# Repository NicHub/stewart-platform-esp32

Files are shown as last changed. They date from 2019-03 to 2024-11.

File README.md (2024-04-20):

# STEWART PLATFORM ON ESP32

<a href="https://archiveprogram.github.com/arctic-vault/">
<table style="border:none">
<tr>
<td>

</td>
<td>
This repository<br/>is archived in the<br/><em>GitHub Arctic Code Vault</em>.
</td>
</tr>
</table>
</a>

<p align="center">
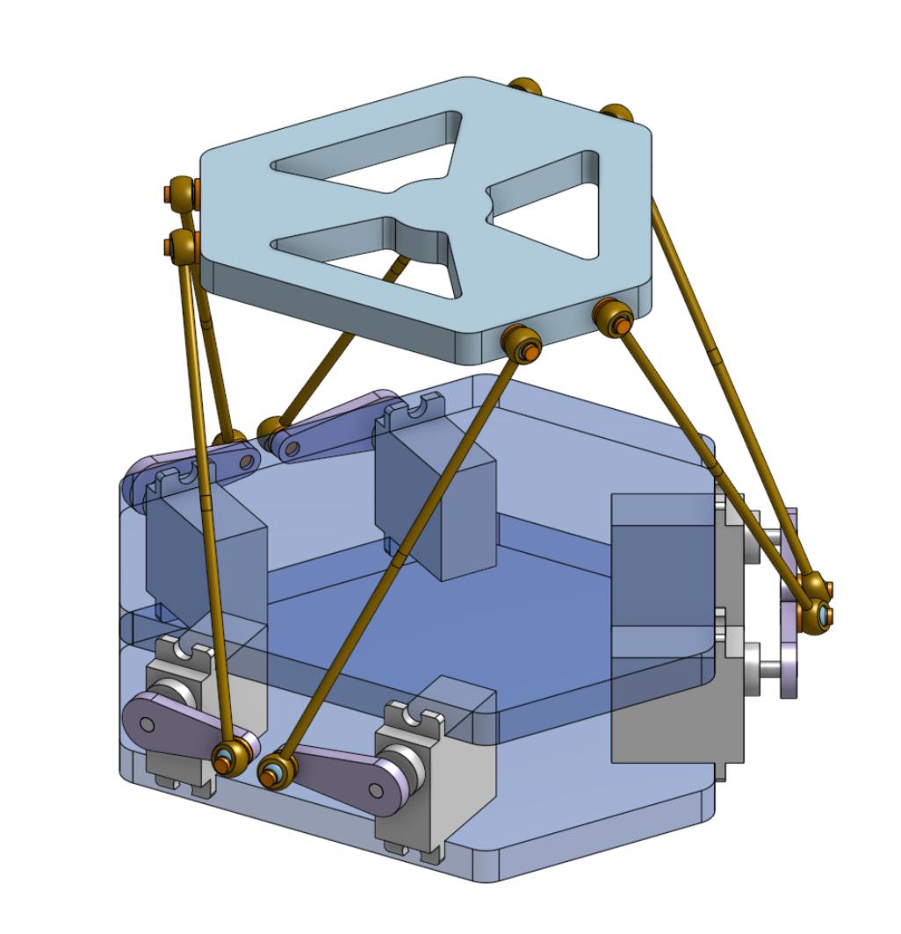
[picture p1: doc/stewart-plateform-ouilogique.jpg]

</p>

## ABSTRACT

This is an ESP32 implementation of a six-degree-of-freedom hexapod — also called _Stewart Platform_, _Gough-Stewart Platform_ or _Parallel manipulator_.
The actuators are PWM rotary servo motors and the program is written in _Arduino C_ compiled with [_PlatformIO_](https://platformio.org/).
This project is done in the frame of the _P19 project_ at the [Microclub](https://microclub.ch).

Currently the platform can be operated:

-   With a _Nunchuck_.
-   With _Arduino C_ code (see [`Hexapod_Demo.cpp`](./src/Hexapod_Demo.cpp)).
-   With _G-Code_ sent by a computer to the ESP through the serial port (see [`python/gcode2serial.py`](./gcode2serial/gcode2serial.py)).

The calculation of the kinematics is performed in [`Hexapod_Kinematics.cpp`](./src/Hexapod_Kinematics.cpp) and can be also be compiled in a desktop C++ program to cross-check calculations (i.e. without actuating the servos).
I managed to compile it with `g++` on _macOS Mojave_ and _macOS Monterey_.
See [`hexapod_desktop_app/hexapod_desktop_app.cpp`](./hexapod_desktop_app_cpp/hexapod_desktop_app.cpp).

## HOME PAGE OF THE PROJECT

The home page is a work in progress, but the video shows what the platform can do.
The original implementation used an analog joystick, but the current version uses a Wii Nunchuck.

The automatic translation in English can be read here:

<https://ouilogique-com.translate.goog/plateforme-de-stewart-esp32/?_x_tr_sl=fr&_x_tr_tl=en>

The original version in French is here:

<https://ouilogique.com/plateforme-de-stewart-esp32/>

## PREREQUISITES

-   Change the default I²C address of the PCA9685 driver from `0x40` to `0x41` by shorting the A0 jumper beside the capacitor.

<p align="center">
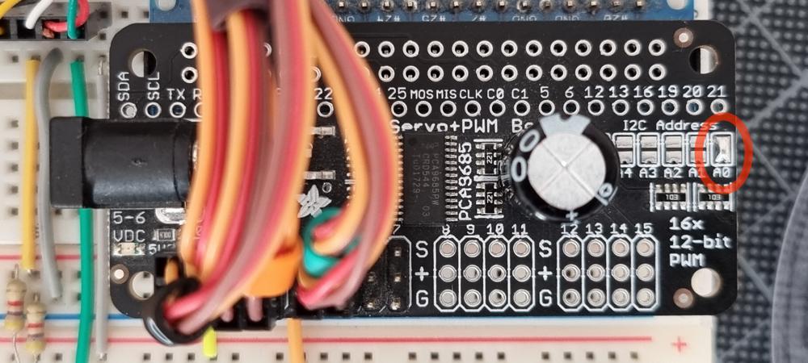
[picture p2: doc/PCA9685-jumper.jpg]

</p>

-   Create a file called `src/WifiSettings.h` containing:

```C++
#pragma once

const char *ssid = "";            // SSID of your WiFi router.
const char *password = "";        // Password of your WiFi router.
const char *ap_ssid = "STEW32-";  // SSID of the ESP32 WiFi network in soft-AP mode (15 char max).
const char *ap_password = "";     // Password of the ESP32 WiFi network in soft-AP mode.
                                  // Must be 8 char min or empty for no password.
```

## GEOMETRY SETTINGS

Geometry settings are defined in
[`Hexapod_Config_1.h`](./src/Hexapod_Config_1.h).

The meaning of the parameters is explained in
[`doc/hexapod-parameters.pdf`](./doc/hexapod-parameters.pdf).

## PARTS TO BUILD

### Base plates

The two base plates are identical and the DXF file to reproduce them is here (right-click + save as):
[`doc/hexapod-base-plate.dxf`](https://raw.githubusercontent.com/NicHub/stewart-platform-esp32/master/doc/hexapod-base-plate.dxf).

<p align="center">
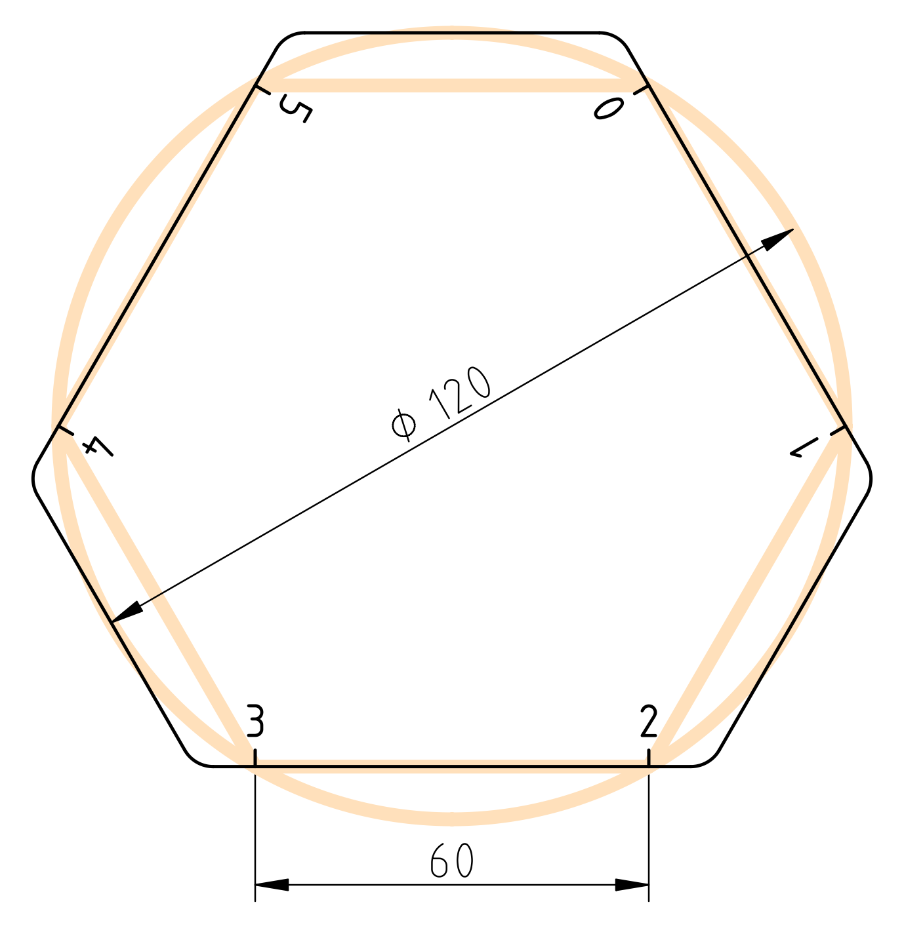
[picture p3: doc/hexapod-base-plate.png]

</p>

### Top plate

The top plate is 3D-printed (right-click + save as):
[`doc/hexapod-top-plate.stl.zip`](https://raw.githubusercontent.com/NicHub/stewart-platform-esp32/master/doc/hexapod-top-plate.stl.zip).

## PARTS TO BUY

| QTY  | PART |
| :--- | :--- |
| 1 | [WeMos ESP32 WROOM](https://www.banggood.com/fr/WeMos-ESP32-WiFi-Bluetooth-Development-Board-Ultra-Low-Power-Consumption-Dual-Core-ESP-32-ESP-32S-p-1175488.html) |
| 1 | [Adafruit PCA9685 16-Channel Servo I²C Driver](https://www.mouser.ch/ProductDetail/adafruit/3416/?qs=F5EMLAvA7ICYzX4Av%252bhRHw==) |
| 1 | [Breadboard adapter for PCA9685](https://www.aliexpress.com/item/1005004132188471.html) |
| 1 | [5 V / 10 A power supply](https://aliexpress.com/af/32810906485.html) |
| 6 | [Rods M3x100mm (140mm total)](https://aliexpress.com/af/32775630549.html) |
| 6 | ¹ [Tower Pro MG996R servo (clone)](https://fr.aliexpress.com/item/32636102294.html) |
| 1 | [Nunchuck](https://fr.aliexpress.com/item/1005003050706988.html) <!-- https://fr.aliexpress.com/item//32880983134.html --> |
| 1 | ² [Nunchuck cable extension](https://fr.aliexpress.com/item/32784720613.html) <!-- https://fr.aliexpress.com/item//32841281892.html --> |
| 1 | ³ [Adafruit Wii Nunchuck Breakout Adapter](https://www.adafruit.com/product/4836) |
| 1 | [6 pin Dupont connector to connect Nunchuck to breadboard](https://www.aliexpress.com/item/32809965211.html) |
| 1 | [Set of cable markers](https://fr.aliexpress.com/item/1005004255868271.html) |
| 6 | [M3×5×6 Brass insert nuts](https://www.aliexpress.com/item/32828848326.html) |
| 12 | Small screws to hold the motors on the base plates |
| 6 | M3×12 screw |
| 6 | M3×12 nut |
| 1 | Breadboard |
| some | Breadboard wires |
| 2 | 4.7 kΩ resistor |

### Notes

-   ¹ I currently use clones of the _Tower Pro MG996R_ servos, but they are bad and I don’t recommend them.
    <https://fr.aliexpress.com/item/32636102294.html><br/>
    I formerly used clones of the _Tower Pro MG90s_ Servos, but they were also bad and too small for this application.
    <https://www.banggood.com/6X-Towerpro-MG90S-Metal-Gear-RC-Micro-Servo-p-1072260.html><br/>
    In the future, I will probalbly use _Parallax 900-00005_ servos.
    It seems that these are the one used by _fullmotiondynamics_ in their videos.
    <https://www.parallax.com/product/900-00005>
-   ² The Nunchuck cable extension is not mandatory.
    The idea is not to have a longer cable but rather to use the extension as an adapter between the Nunchuck and the breadboard, that is to say that it allows to leave the Nunchunk cable uncut.
-   ³ This breakout adapter is not mandatory, but it could simplify wiring.
    I haven’t used it myself.

## WIRING

### Nunchuck

> The Nunchuck library uses `Wire.h` and standard I²C connections internaly.
>
> Pins are seen from left to right and top to bottom looking at the Nunchuck connector.
>
> Cut the cable extension to connect to the ESP32.

| color  | signal | ESP32 pin |
| :----- | :----- | :--- |
| white  | SCL | IO22 |
| NC | | |
| red | GND | GND |
| green  | VCC | VCC |
| black  | ATT | IO32 (or connect to 3.3V to force Nunchunk detection) |
| yellow | SDA | IO21 |

## EXTERNAL LIBRARIES

The external libraries are installed automatically during the first build because they are declared under `lib_deps` in `platformio.ini`.

## I²C ADDRESSES

> By default, the PCA9685 driver and the Nunchuck share the same I²C address `0x40`.
> Fortunately, the address of the PCA9685 driver can easily be changed to `0x41` by shorting the A0 jumper next to the capacitor.

| Default address | New address | Device |
| :--- | :--- | :--- |
| 0x40 | 0x41 | PCA9685 |
| 0x70 | = | PCA9685 (broadcast) |
| 0x40 | = | Nunchuck ([IMU](https://en.wikipedia.org/wiki/Inertial_measurement_unit)) |
| 0x52 | = | Nunchuck (joystick) |
| 0x68 | = | GY-91 (MPU9250) |
| 0x76 | = | GY-91 (BMP280) |

## CREDITS

### My sources of inspiration

-   San-José State University / Full Motion Dynamics:
    -   <https://www.youtube.com/watch?v=j4OmVLc_oDw>
    -   ~~fullmotiondynamics.com~~

### Kinematics

-   Hexapod kinematics of this project was originaly based on _6dof-stewduino, by Philippe Desrosiers_, althought I reworked it in depth:
    -   <https://github.com/xoxota99/stewy>
-   He derived his implementation from the work of _Daniel Waters_:
    -   <https://www.youtube.com/watch?v=1jrP3_1ML9M>
-   Kinematics calculation is also explained in this document by an unknown author from the _Wokingham U3A Math Group_:
    -   <https://memememememememe.me/assets/posts/stewart-platform-math/MathsOfStewartPlatformV5.pdf>
    -   <http://www.wokinghamu3a.org.uk/groups/mathematics/>
-   The project _memememememememe_ was also an excellent source of inspiration.
    They share the code for _RPi_ and a simulator in the _Processing_ langage:
    -   <https://memememememememe.me/post/stewart-platform-math/>
    -   <https://github.com/thiagohersan/memememe>

### Serial buffer for G-Code

-   Derived from _MarginallyClever_:
    -   <https://github.com/MarginallyClever/GcodeCNCDemo/tree/master/GcodeCNCDemo4AxisCNCShield>

## FURTHER READINGS

-   PID Control System Analysis and Design, By YUN LI, KIAM HEONG ANG, and GREGORY C.Y. CHONG
    -   See Table 1, p.33 <http://eprints.gla.ac.uk/3815/1/IEEE_CS_PID_01580152.pdf>
-   Understanding PID Control, Part 1: What is PID Control?
    -   <https://www.youtube.com/watch?v=wkfEZmsQqiA>
-   Modern Robotics, Chapter 7: Kinematics of Closed Chains
    -   <https://youtu.be/5wCK6XGC3ig>

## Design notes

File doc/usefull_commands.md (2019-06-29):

# PLATFORMIO COMMANDS

## Build
ctrl + alt + b

## Upload
ctrl + alt + u

## Serial Monitor
ctrl + alt + s

## SPIFFS Data Upload
In terminal, run:

    platformio run --target uploadfs

## Clean build
platformio run --target clean

# Problème WiFi
ESP32 Brownout detector was triggered

# GIT COMMAND
git update-index --skip-worktree ./hexapod_desktop_app/hexapod_desktop_app

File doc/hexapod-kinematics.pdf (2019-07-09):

FORWARD KINEMATICS SOLUTION OF A STEWART PLATFORM ACTUATED BY ROTARY MOTORS (DRAFT)

NICOLAS JEANMONOD, OUILOGIQUE.COM, MAY 2019

Part 1. Abstract

This paper presents an algorithm for the calculation of the forward kinematics solution of a Stewart platform actuated by rotary motors. It is based on the following paper by an unknown author from the Wokingham U3A Math Group: https://bit.ly/2FU3rUJ. (https://web.archive.org/web/20130506134518/http://www.wokinghamu3a.org.uk/Maths%20of%20the%20Stewart%20Platform%20v5.pdf) This algorithm has been implemented on an ESP32 microcontroller: https://github.com/NicHub/stewart-platform-esp32.

Part 2. Positions of the platform joints Pi relative to the servo pivots Bi

Let’s consider an orthogonal system of axis xyz with origin in the middle of the moving platform and the z axis pointing downwards. The coordinates of the platform joints are called Pi where i = motor index = 0..5. Note that at home position P zi = 0.
Pi = {P xi
, P yi

, 0, 1}
The platform has six degrees of freedom, three rotations and three translations with the following transformation matrices:

Rx =

1 | 0 | 0 | 0
0 | cos A sin A 0
0 − sin A cos A 0
0 | 0 | 0 | 1

Ry =

cos B 0 − sin B | 0
0 | 1 | 0 | 0
sin B | 0 | cos B 0
0 | 0 | 0 | 1

Rz =

cos C | sin C | 0 0
− sin C | cos C 0 0
0 | 0 | 1 0
0 | 0 | 0 1

T xyz =

1 | 0 | 0 | 0
0 | 1 | 0 | 0
0 | 0 | 1 | 0
T x T y T z 1

The servo pivots have the following coordinates.

Bi = {Bxi
, Byi

, Zhome, 1}
Translation of servo pivots Bi relative to the origin:

T B =

1 | 0 | 0 | 0
0 | 1 | 0 | 0
0 | 0 | 1 | 0
−Bx −By −Zhome 1

The positions of the platform joints Pi relative to the servo pivots Bi after movement are called BPi and can be found by calculating the dot product below. Note that the result is the solution of the forward kinematics of platforms actuated by linear motors.

BPi = Pi

- Rx · Ry · Rz · T xyz · T B =

(1)

BP xi
BP yi
BP zi
1

T

=

P xi cos B cos C + P yi (sin A sin B cos C − cos A sin C) + T x − | Bxi
P xi cos B sin C | + P yi (sin A sin B sin C + cos A cos C) + T y − | Byi
−P xi sin B | + | P yi sin A cos B | + T z | − Zhome
| | 1

T

1

FORWARD KINEMATICS SOLUTION OF A STEWART PLATFORM ACTUATED BY ROTARY MOTORS (DRAFT) | 2

Part 3. Rotation of the vector BP in the plane of the servo arm

The arm plane is rotated by a negative angle Θs and it defines a new system of coordinates that is also rotated. Let’s find the coordinates of BP in this new reference system:

BP xi
BP yi
BP zi
1

T

·

cos Θs | sin Θs | 0 0
− sin Θs | cos Θs | 0 0
0 | 0 | 1 0
0 | 0 | 0 1

=

cos ΘsBP xi − sin ΘsBP yi
sin ΘsBP xi + cos ΘsBP yi
BP zi
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
In the original algorithm, Θs is positive, so we can rewrite:

(2)

a
b
c
1

T

=

cos ΘsBP xi + sin ΘsBP yi
− sin ΘsBP xi + cos ΘsBP yi BP zi
1

T

Part 4. Intersection between servo arm circle and rod sphere in the plane of the servo arm circle

The end of the rod is somewhere on a sphere. This sphere will intersect the circle of the servo arm 0, 1 or 2 times. This circle lies in a plane which has two axis x and z, so y = 0. This plane is rotated by an angle Θs along the z axis. We applied the rotation to the BP vector in the previous section to find the values of a, b and c. The rotation implies that BP is in the negative region of y and that explains the sign of the term +b

2
in the equation of the sphere below.
Now we will find the intersection of the rod sphere and the arm circle. The circle is expressed in parametric coordinates, but is also possible to solve this problem by expressing it in Cartesian coordinates.

(x − a)

2 + b
2 + (z − c)
2 | = rod²
arm cos ϕ | = x
arm sin ϕ | = z

(arm cos ϕ − a)

2 + b
2 + (arm sin ϕ − c)

2 = rod²

arm²

cos² ϕ − 2 arm cos ϕ a + a

2
+

arm²

sin² ϕ − 2 arm sin ϕ c + c
2
= rod² − b | 2
cos² ϕ − 2

a
arm

cos ϕ +

a

2
arm²
+
sin² ϕ − 2

c
arm

sin ϕ +

c

2
arm²
=
rod² − b | 2
arm²

d =

a
arm
e =

c
arm

cos² ϕ − 2d cos ϕ + d

2
+

sin² ϕ − 2e sin ϕ + e
2
=
rod² + b | 2
arm²
cos² ϕ + sin² ϕ = 1

d cos ϕ + e sin ϕ =

1
2
1 + d | 2 + e 2 −

rod² − b

2
arm²

d cos ϕ + e sin ϕ =

1
2

arm²
arm²

+

a

2
arm²

+

c

2
arm²

−

rod² − b

2
arm²

d cos ϕ + e sin ϕ =

a

2 + b

2 + c

2 + arm² − rod²
2 arm²

= f

FORWARD KINEMATICS SOLUTION OF A STEWART PLATFORM ACTUATED BY ROTARY MOTORS (DRAFT) | 3

Identity

m sin α + n cos α = o sin (α + p)

o =

p
m² + n²

tan p =

n
m
n cos α + m sin α = ±

p

m² + n² sin
α + arctan

n
m

if −

π
2

< arctan

n
m

<

π
2

then

n cos α + m sin α =

p

m² + n² sin
α + arctan

n
m
= f

Thus

f =

p
d

2 + e

2 sin
ϕ + arctan

d
e

ϕ = arcsin

f
√
d

2 + e

2

− arctan

d
e

ϕ = arcsin

a

2+b

2+c

2+arm²−rod²
2 arm² q

a²
arm² +

c

2
arm²

− arctan

a
c

ϕ = arcsin

a

2 + b

2 + c

2 + arm² − rod²
2 arm√
a

2 + c

2

− arctan

a
c

ϕ = arcsin

a

2 + b

2 + c

2 + arm² − rod²

2 · arm · c ·

q
1 +

a
c

2

− arctan

a
c

The length of the vector BP is the same in both systems of coordinates (arm and platform). So we calculate it in the platform system because this allows us to drop the calculation of b:

a

2 + b

2 + c

2 = BP²

x + BP²
y + BP²

z = BP²
(3)

ϕ = arcsin

BP² + arm² − rod²

2 · arm · c ·

q
1 +

a
c

2

− arctan

a
c

(4)

The angle ϕ equals 0 when the arm is horizontal, but we want it to be 0 when the arm is at half of its full angular range:

(5) ϕf inal = ϕ +

servo full angular range
2

Part 5. Conversion from radian to PWM microseconds and mirroring

The conversion of the angle in radian to an angle expressed in PWM microseconds is done with a simple linear relation that is different for odd and even servomotors:

(6) ϕPWMµs =

(
gain · ϕf inal + servo min pwm µs + offset −gain · ϕf inal + servo max pwm µs + offset

where

(7) gain =

servo max pwm µs − servo min pwm µs servo full angular range rad
A typical value for the gain is (2000 − 1000) /π ≈ 318 µs/rad ≈ 5.6 µs/◦ .

FORWARD KINEMATICS SOLUTION OF A STEWART PLATFORM ACTUATED BY ROTARY MOTORS (DRAFT) | 4

The offset will be typically 0, but can be adjusted to take into account that the arms cannot be mounted exactly at the correct angle. The sign of gain takes into account the fact that the odd and even arms are a reflection of each other. Thus, odd and even servomotors must have opposite gain values.

Part 6. Calculation of Zhome

Zhome must be calculated for each platform geometry so that when the platform is at home position, i.e. with no translation and no rotation, the arms are horizontal or tilted at any value that makes sense.
TO DO: calculation of Zhome.

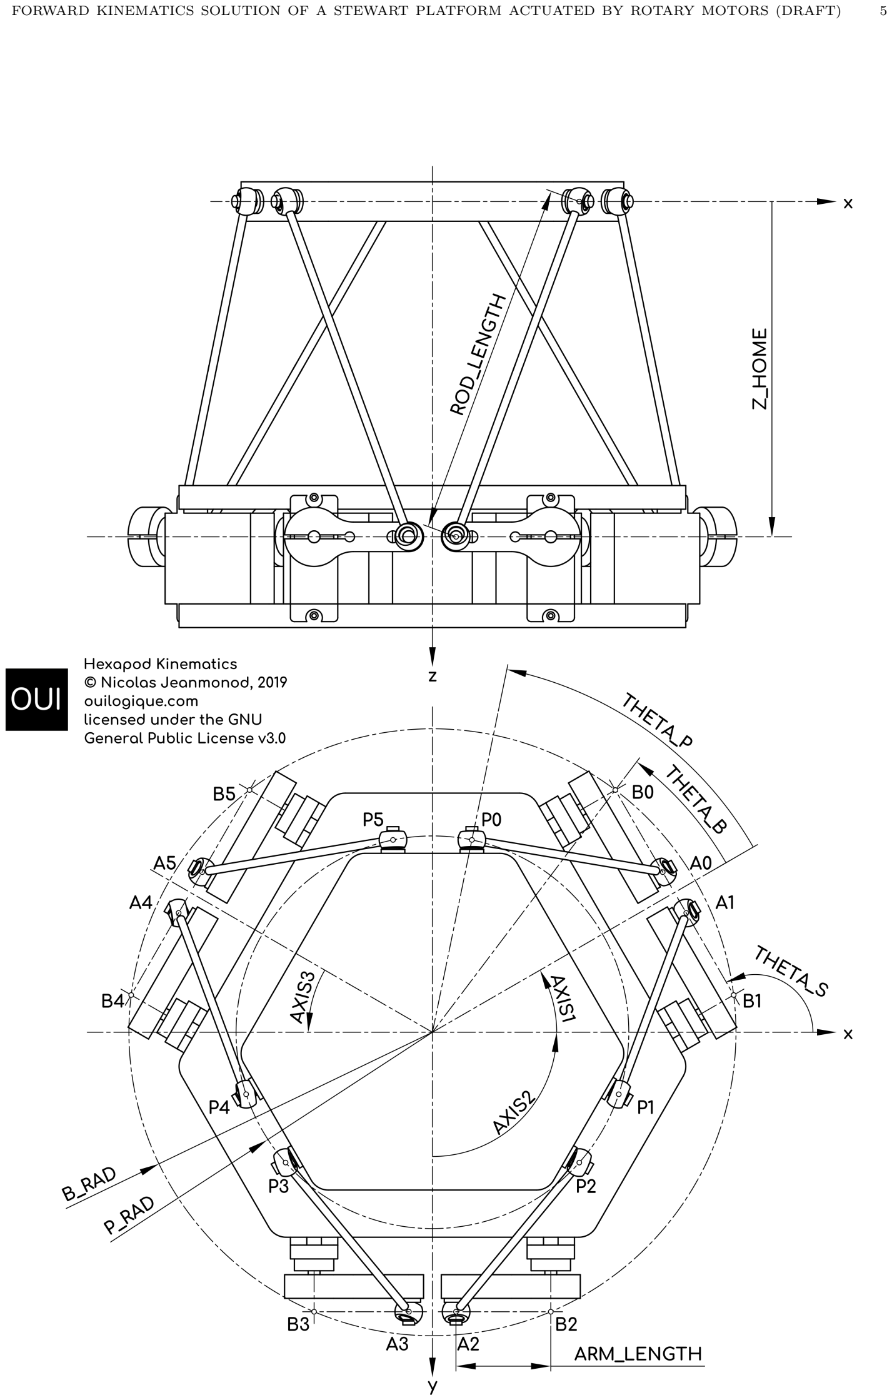
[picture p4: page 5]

FORWARD KINEMATICS SOLUTION OF A STEWART PLATFORM ACTUATED BY ROTARY MOTORS (DRAFT) | 5

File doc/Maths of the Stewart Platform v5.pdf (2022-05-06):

## The Mathematics of the Stewart Platform

The Stewart Platform consists of 2 rigid frames connected by 6 variable length legs.

The Base is considered to be the reference frame work, with orthogonal axes x, y, z.

The Platform has its own orthogonal coordinates x’, y’, z’.

The Platform has 6 degrees of freedom with respect to the Base

The origin of the Platform coordinates can be defined by 3 translational displacements with respect to the Base, one for each axis.

Three angular displacements then define the orientation of the platform with respect to the Base. A set of Euler angles are used in the following sequence:

1. Rotate an angle ψ (yaw) around the z-axis
2. Rotate an angle θ (pitch) around the y-axis
3. Rotate an angle (roll) around the x-axis

If we consider the first rotation ψ (yaw) around the z-axis:

P = i’x’ + j’y’ + k’z’ = ix + jy + kz

x = OA – BC

= x’cos ψ – y’sin ψ

y = AB + PC

= x’sin ψ + y’cos ψ

z = z’

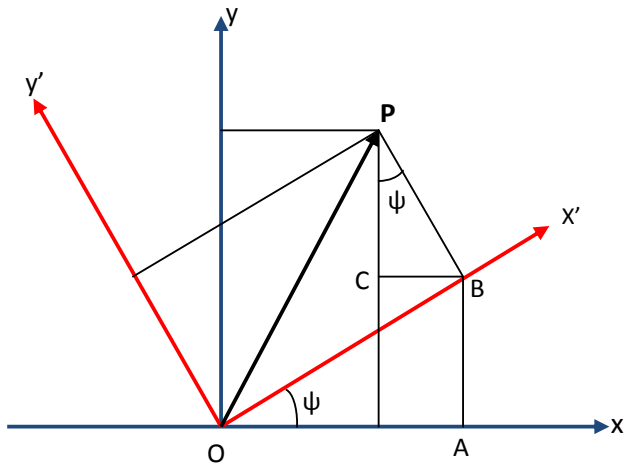
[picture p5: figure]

We define the rotation matrix | where

=

and | =

Similarly If we consider the second rotation θ (pitch) around the y-axis we can show

=

,

And for the third rotation (roll) around the x-axis:

=

The full rotation matrix of the Platform relative to the Base is then given by:

=

=

=

=

- (1)

Now consider a Stewart Platform.

For the

leg:

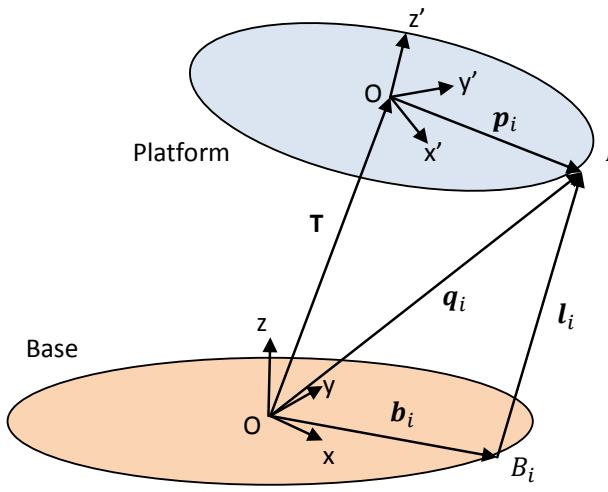
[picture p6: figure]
Platform; Base

The coordinates | of the anchor point | with respect to the Base reference framework are
given by the equation

= T +

- (2)

Where T is the translation vector, giving the positional linear displacement of the origin of the Platform frame with respect to the Base reference framework, and

is the vector defining the coordinates of the anchor point with respect to the Platform framework.

Similarly the length of the

leg is given by

| = T +

- (3)
| where is the vector
defining the coordinates of the lower anchor point
| . These 6 equations give the lengths
of the 6 legs to achieve the desired position and attitude of the platform.

When considering the Forward Kinematics, this expression represents 18 simultaneous non-linear equations in the 6 unknowns representing the position and attitude of the platform. Much work has been done on finding the solutions to these equations; in the general case there are 40 possible solutions, although in practice many of these solutions would not be practical.

If the leg lengths are achieved via rotational servos, rather than linear servos, a further calculation is required to determine the angle of rotation of the servo. Each servo / leg combination can be represented as follows:

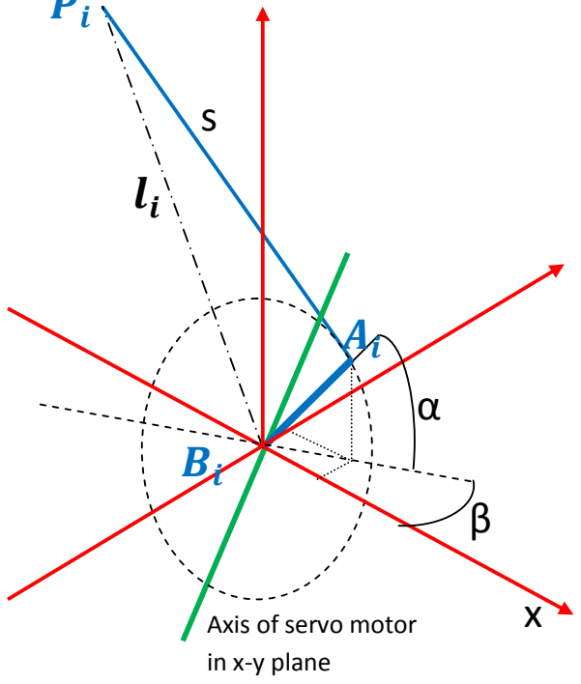
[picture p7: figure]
Axis of servo motor in x-y plane

y

z

Where: a = length of the servo operating arm

are the points of the arm/leg joint on the

servo with coordinates

=

in the base framework.

are the points of rotation of the servo arms with the coordinates

=

in the base framework.

are the points the joints between the operating rods and the platform,

with coordinates | =

in the platform framework

S = length of operating leg

= length of the
leg as calculated from

= T +

α = angle of servo operating arm from horizontal

β = angle of servo arm plane relative to the x-axis. Note that the shaft axis lies in the x-y plane where z = 0

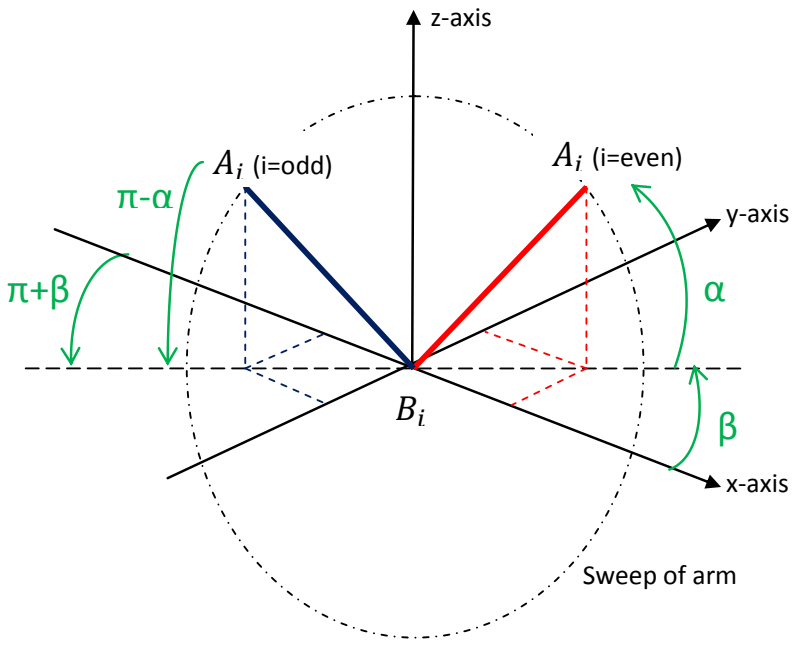
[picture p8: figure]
z-axis; y-axis; x-axis; Sweep of arm; (i=even); (i=odd)

Point is constrained to be on the servo arm, but the arrangement of the servos means that the odd and even arms are a reflection of each other. So for the even legs we have:

= a | , and | - (4)
= a | , and | - (5)

= a | - (6)

And for the odd legs we have:

= a | , and
= a | , and

= a

But | = | , and | =
And | = | , and | =

Substituting these values into the equations for the odd legs, we get the same equations as (4), (5), and (6) for the even legs.

By Pythagoras we also have:

=

+

+

=

+

- 2
- (7)

=

+

+

=

+

- 2 | - (8)

=

+

+

=

+

- 2

And substituting from equations (7) & (8)

=

+ 2 | +

+
2
- 2

re-arranging gives

= 2

+ 2 | + 2 | + 2 | –
2
And substituting for | , | , | from equations (4), (5) & (6) then gives

= 2

+ 2

+
2

+ 2

2

= 2

+ 2 | + 2 | - 2

+
2a | + 2 | - 2
+ 2a | + 2 | -
2

Which reduces to

= 2a | 2 | + 2a
= 2a | 2a

Which is an equation of the form:-

L =

Using the Trig identity for the sum of sine waves

where

and

We therefore have another sine function of α with a phase shift δ

L = | where | δ =
Therefore | =
And | α =

- (9)

where L =

M = 2a

N = 2a

We now have sufficient information to calculate the lengths of the effective “legs”, and the associated angle of the servo arms, for the reverse kinematics for the platform. But to design and implement the hexapod platform we need to define a few constants in order to define the range of movement.

1) We need to define the “home” position of the platform. By definition this will be where the platform is at a height above the base framework, and there being no other translational or rotational movement.

i.e.

= T +

=

=

Similarly we will define the “home” position where the servo arms and rods are at right angles to each other.

i.e.

=

Giving

- (10)

and since the platform is constructed symmetrically around the z-axis, this equation will give the same result for any leg.

2) We can also calculate the angle of the servo arm at the Home position.

Using the equation

= T +

And remembering the symmetrical construction of the platform. The length of the legs in the “home” position is given by

- (11)

And the angle of the servo arm in the “home” position can be given by equation (9). Since we have symmetry, we can look at leg 2 only, where β = 0°.

=

- (12)

where =

= 2

| = 2a
| = 2a
| = 2a

The servos are mounted so that their mid point is close to the “home” position, and we will restrict their movement to ± 45°. The servos are controlled by a pulse whose duration defines the angle of the arm.

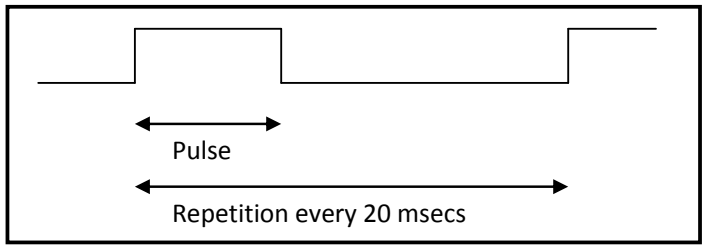
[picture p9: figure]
Pulse; Repetition every 20 msecs

The servos used have the specification:

Neutral position (“home”) is nominally 1500µsecs

Rotation clockwise for increasing pulse width

Pulse width change for 45° is 400 µsecs giving a servo rate,

r =

=

µsecs / radian

From the above, the pulse widths

for each of the servos can be obtained by the equations:

for even i and | -(13)
for odd i | - (14)

Where

is the actual pulse width required to hold the | servo in the “home”
position. This is nominally 1500µsecs, but can be adjusted to compensate for differences in actual assembly.

## Controlling the Stewart Platform using RC Servos

The platform is constructed with symmetry round the z-axes, but the odd and even servos are mounted in opposition.

The circuitry used to control the platform is based on a PICAXE microcontroller with attached maths co-processor (floating point) and attached servo motor controller.

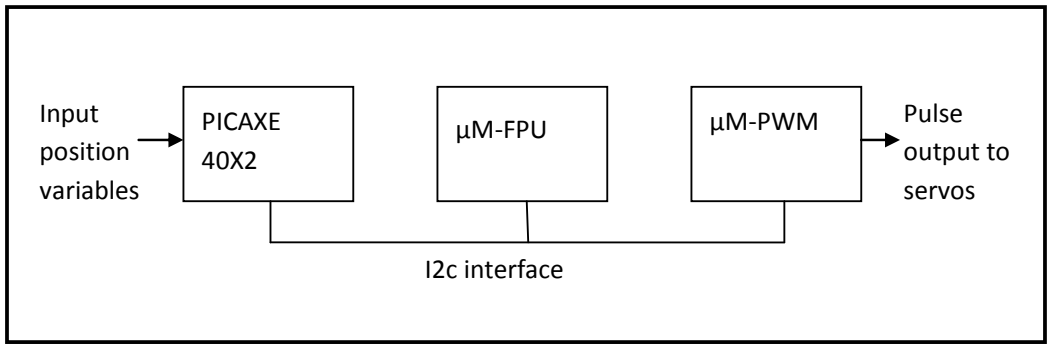
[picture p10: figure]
PICAXE 40X2; µM-FPU; µM-PWM; I2c interface; Input position variables; Pulse output to servos

The sequence of events is as follows:

1) Input the positional information for the platform,

s, a,

. These are all
constants from the build of the platform.
2) Input the constants for the servo motors,

and r
3) Calculate the values of | from equation (10), and | from equation (12)
4) Input the variables for (x, y, z, ψ, θ, φ) for the required platform position
5) Calculate the rotational matrix

from equation (1)
6) Calculate the effective leg lengths
from equations (3)
7) Calculate the angles

required for each servo from equation (9)
8) Calculate the pulse widths

required for each servo from equations (13) & (14)
9) Output the values of

to the µM-PWM to drive the servos
10) Return to step 4) to repeat the process.

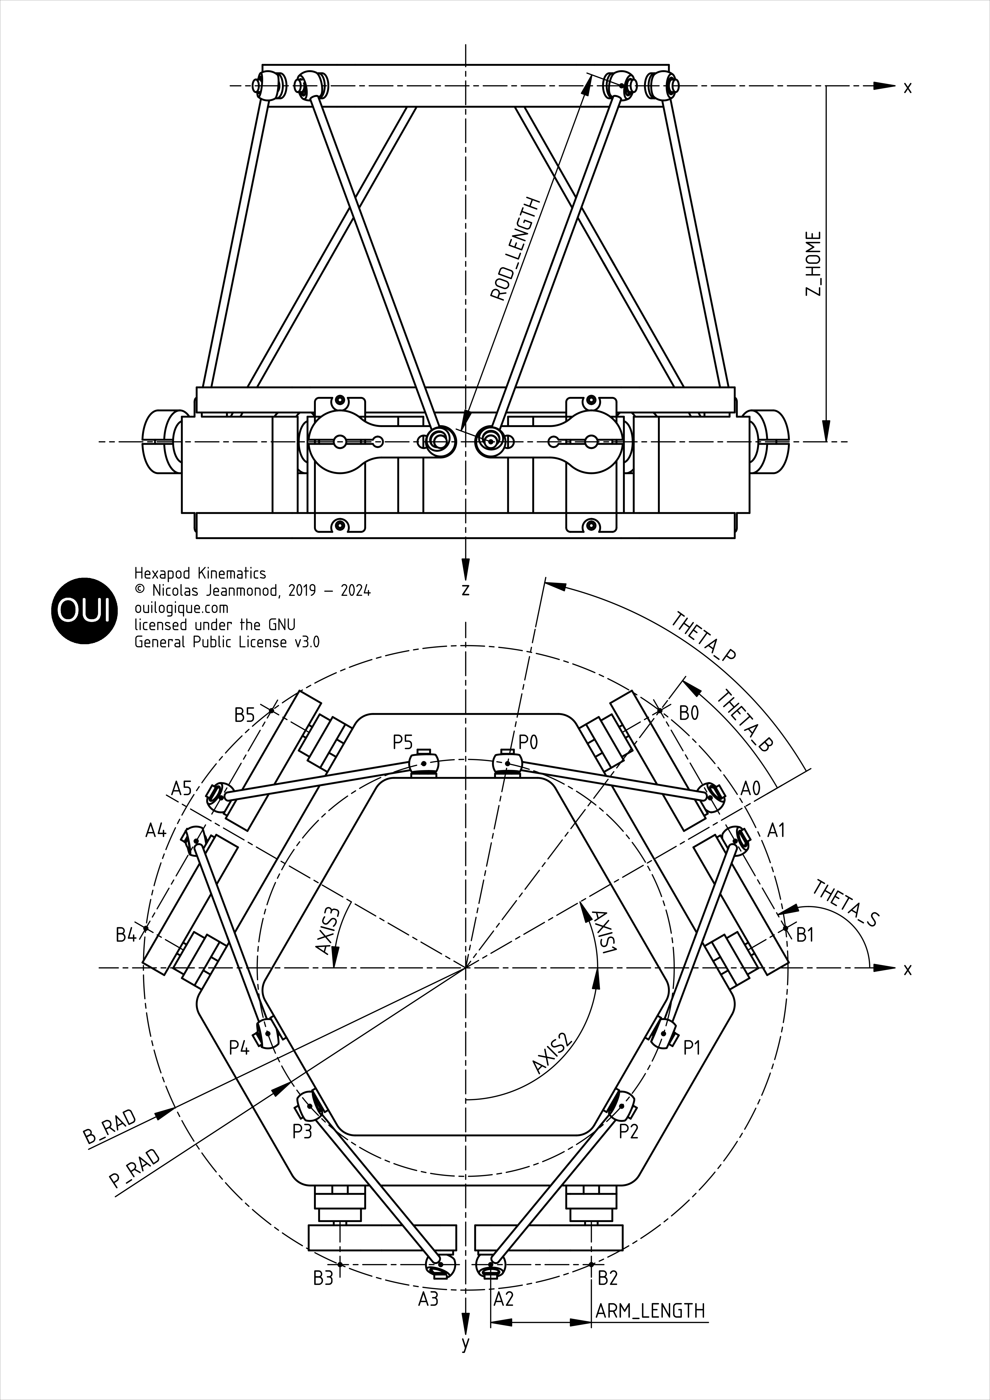
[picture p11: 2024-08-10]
doc/hexapod-parameters.png

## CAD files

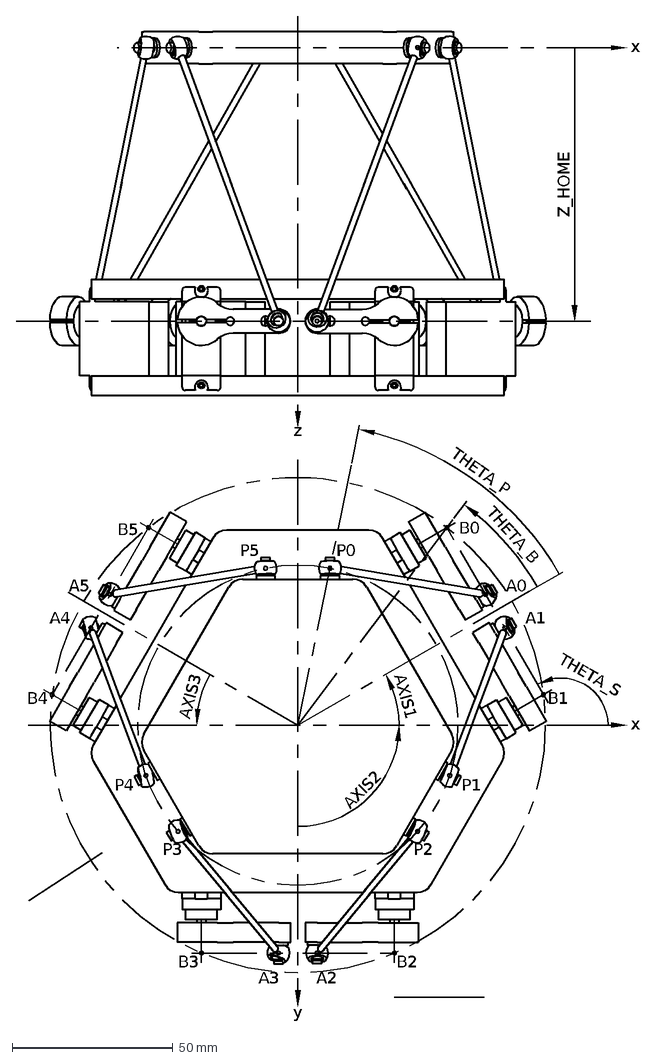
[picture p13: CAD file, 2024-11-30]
doc/hexapod-parameters.dxf
B0
B1
B2
B3
B4
B5
P0
P4
P2
P5
P3
P1
x
z
A0
A1
A2
A3
A5
A4
Z_HOME
y
THETA_B
THETA_P
THETA_S
AXIS3
AXIS1
AXIS2

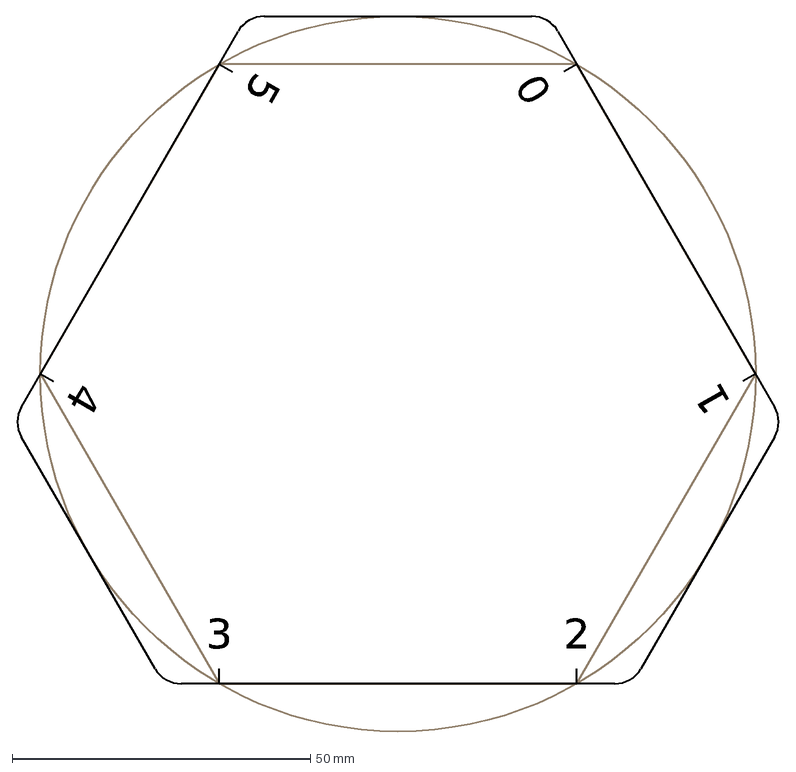
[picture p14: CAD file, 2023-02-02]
doc/hexapod-base-plate.dxf
3
1
2
0
4
5

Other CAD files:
doc/hexapod-top-plate.sldprt

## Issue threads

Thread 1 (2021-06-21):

stewart-platform-esp32

hassanvvvvv, 2021-06-21:
Hello
I run the project "stewart-platform-esp32"  but it does not work properly. In this way, when I move the joystick, no pulse is generated and the servo motors do not move at all.
Help me, please.

Closed 2021-12-26.

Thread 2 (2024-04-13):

Troubleshooting Stewart platform.

Jesseforeman3825, 2024-04-13:
Thanks for offering to help! I’ve been at this for days. I didn’t know if I would be able to reach you. I have been reading through the code and can’t for the life of me figure out what I’m doing wrong. Here is a picture of the lay out on the breadboard I tried to mimic what you setup as close a possible. I changed the colors of the nunchuck wires plugging into the board when I soldered on my leads for connecting to the breadboard. That way I was easier for me to tell where the wires needed to go.  The only thing in the code that comes up highlighted in yellow after compiling is this MLPrintLog and a few things related to that. But it still uploads.  When  I power  the esp32 with a usb cable and power  the pwm driver  (5v 10a) it doesn’t move or home. I’m so glad you reached back out to me. thank you so very much!! Maybe with your help I’ll be able to get this going.
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
![Uploading image.jpg…]()

NicHub, 2024-04-13:
Hi Jesse, nice job. In order to check your wiring, can you scan your i²c bus with this:

https://github.com/NicHub/i2c_scanner

The scanner should say:

```
Scanning I2C bus...
0x41
0x52
Number of I2C devices found: 2
```

Jesseforeman3825, 2024-04-13:
I’m new to platformio. I created a new workspace and uploaded the i2c scanner then went to the serial monitor and I got it to communicate back one time saying there wasn’t any i2c devices found trying to run it again and I’m not getting anything back at all like it’s hung up. I’m doing something wrong.
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

Jesseforeman3825, 2024-04-13:
I had to hit the button on the esp32 for it to run.. had no idea. This is what came back tho.
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

Jesseforeman3825, 2024-04-13:
I tested continuity between the sda/ scl pins and the pwm driver as well as the nunchuck everything is is connected the pwm driver is getting power from both 3v the esp32 and the 5v supply. The nunchuck is getting 3v power also. The nunchuck gets a little warm after a while of being plugged in idk if that’s normal or not. So strange I feel like it should work. Lol I designed and machined my platform in aluminum.  I want to put interchangeable ball mazes on in. It looks like the 3rd button click on the nunchuck makes it pitch and roll like I would want.  I really like how you set everything up. Everything seems so straight forward. I’ll keep playing around it seems like it must be a hardware issue.

NicHub, 2024-04-14:
OK, I’ve checked your wiring and from what I can see, it’s correct. The only difference I can see is the white wire connected from IO4 to VCC, which is not necessary but shouldn’t do any harm either. For the time being, it’s best to remove it.

I searched the internet for the error you get
`[E][esp32-hal-i2c.c:1434] i2cCheckLineState(): Bus Invalid State, TwoWire() Can’t init sda=0, scl=0
Number of I2C devices found: 0`
and I found this page: https://github.com/espressif/arduino-esp32/issues/3079
There seems to be an electrical problem.

You also said that your Nunchunk was heating up, and I think that this is not normal. The first thing to do is remove the Nunchunk, plug in the PCA9685 driver only and scan the I²C again. The scanner should find a device at 0x41. If it finds it at 0x40, this means you need to change the I²C of the PCA9685 driver. See:

https://github.com/NicHub/stewart-platform-esp32?tab=readme-ov-file#prerequisites

If the PCA9685 driver is found, you can connect the Nunchuck alone. If it can’t be found, consider buying a Breakout adapter: https://www.adafruit.com/product/4836

You can also improve the robustness of the wiring by grouping the Nunchuck pins together with a 5 or 6 pin housing connector: https://www.aliexpress.com/item/1005006051227218.html.

Jesseforeman3825, 2024-04-14:
I already had one of the Adafruit adapters for the nunchuck for the project
so I plugged that in and the address showed up with one device. I then
tried another pwm driver and I have that operational now also. I uploaded
the sketch and now the steppers home.  Progress!! But the nunchuck won’t
operate. I’ve tried clicking all the buttons and moving the stick. Maybe
there is something I need to uncomment? Also it appears there are 3 device
addresses. I’m guessing the adafruit board for the nunchuck has an address
of its own? We are getting there :)

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

NicHub, 2024-04-14:
If you see 3 I²C addresses, that is probably because the scanner discovered the Nunchuck IMU (inertial measurement unit). In my case the scanner finds only the joystick part of the Nunchuck. I documented the addresses here:

https://github.com/NicHub/stewart-platform-esp32?tab=readme-ov-file#ic-addresses

---

In `platformio.ini` you can set `SEND_NUNCHUCK_INFO_TO_SERIAL=true` and check in the serial monitor if you get some outputs like below. Set back to `SEND_NUNCHUCK_INFO_TO_SERIAL=false` when you’re done, because this slows down the ESP.

`joy_x = -0.09 | joy_y = 0.09 | btn_c = 0 | pitch_angle = 0.00 | roll_angle = -0.02 | joyMode = 0`

---

In `main.cpp`, you can also add some demo at start below `demoMov_circles`:

```
    hx_demo.demoMov_circles(DEMO_CIRCLES_NB_TURN);
    hx_demo.demoMov_MinMaxAllAxis();
    hx_demo.demoMov_shakeHeave();
```

---

You can also test if the platform can be operated with gcode program. Change the settings in `platformio.ini`: `ENABLE_SERIAL_READ=true` then open a terminal, go to the `gcode2serial` directory and launch the python program that send the gcode commands to the platform. You’ll need to change `<SERIAL PORT>` with the ESP32 serial port, i.e. something like COMx, where x is a number.

```
cd <gcode2serial>
py gcode2serial.py -p <SERIAL PORT> -f demo_123.gcode
```

Jesseforeman3825, 2024-04-14:
I get a message in the serial monitor that says “NUNCHUCK NOT CONNECTED!
ABORTING”

When I ran the i2c scanner again with it shows up with 2 addresses
when using a non Nintendo nunchuck and 16 with a Nintendo original
nunchuck. Both sticks give me the same serial monitor message saying
nunchuck not connected…

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

NicHub, 2024-04-14:
@VeridisQuo555 had the same problem. The solution is here:

https://github.com/NicHub/stewart-platform-esp32/commit/70c877b3a3799f55ff35377e91e9853d12088188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

NicHub, 2024-04-14:
I’ve updated the photos showing the wiring. I’ve removed the red wire that wasn’t serving any purpose and added a 10 µF capacitor. It allows the ESP to be flashed without having to press the BOOT button.

https://ouilogique.com/files/2019-03-27-plateforme-de-stewart-esp32/images/2024-04-14-proto-plateforme-de-stewart_001.jpg

https://ouilogique.com/files/2019-03-27-plateforme-de-stewart-esp32/images/2024-04-14-proto-plateforme-de-stewart_002.jpg

Jesseforeman3825, 2024-04-14:
I hooked up the 3v out on the nunchuck breakout to the IO4 and still get
the same message.

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

NicHub, 2024-04-14:
Then in `Hexapod_Nunchuck.cpp` add `return;` at the beginning of `void Hexapod_Nunchuck::stopIfNotConnected()`. This will disable the Nunchuck presence check.

Jesseforeman3825, 2024-04-14:
I hooked the 3v output pin on the nunchuck breakout to IO35 that’s how you
have it configured in hexapod_nunchuck.cpp
Now it’s working great!! Thanks so much for all the help. Do you have a
PayPal account, or a way I can donate you some money for your work?
On Sun, Apr 14, 2024 at 10:59 AM NicHub
***@***.***> wrote:

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

NicHub, 2024-04-14:
Oops, I actually said it was pin IO4 when it’s actually pin IO35. Thanks for seeing the error. I modified the README file accordingly:

https://github.com/NicHub/stewart-platform-esp32/commit/465158052f087d228912452f70813cfca209f2d7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

Thank you also for offering to give me a donation, it’s the first time it’s happened to me and it makes me super happy. Here’s the link to transfer money to my PayPal account:

https://paypal.me/NicolasJeanmonod

I am also glad to read that the project works for you. For the future, it would be great if you could fork the project so that the community can see how your version is evolving.

https://docs.github.com/en/pull-requests/collaborating-with-pull-requests/working-with-forks/fork-a-repo

You could also set up a blog to publish photos and videos, like me on ouilogique.com.

https://docs.github.com/en/pages/setting-up-a-github-pages-site-with-jekyll

As an example, you can read the translation of my page on the Stewart Platform here:

https://ouilogique-com.translate.goog/plateforme-de-stewart-esp32/?_x_tr_sl=fr&_x_tr_tl=en

Jesseforeman3825, 2024-04-14:
I sent you some money so check your PayPal. I really appreciate your hard
work. This is a stellar project to share with the world expecting nothing
in return.  You should be rewarded for your skills , efforts, and
generosity. I’ll definitely consider posting the platform in its final form
once it’s all done. I’m going to make a pcb for it all and mount it onto my
platform. Thanks so much again for the help. How would I go about inverting
the forward backward movements? (So it’s not like flying a plane)

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

Jesseforeman3825, 2024-04-14:
The pitch up and down is what I’d like to invert.

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

NicHub, 2024-04-14:
You can invert the coordinates in `Hexapod_KinematicsCalcServoAnglesAlgo3.cpp` at the beginning of `Hexapod_Kinematics::calcServoAngles`.
To make it like flying plane, I guess you need to invert roll and pitch. Check it out.

```
int8_t Hexapod_Kinematics::calcServoAngles(platform_t coord, angle_t servo_angles[])
{
    // coord.hx_x = -coord.hx_x; // Invert Surge
    // coord.hx_y = -coord.hx_y; // Invert Sway
    // coord.hx_z = -coord.hx_z; // Invert Heave
    coord.hx_a = -coord.hx_a; // Invert Roll
    coord.hx_b = -coord.hx_b; // Invert Pitch
    // coord.hx_c = -coord.hx_c; // Invert Yaw

    ...
```

NicHub, 2024-04-15:
@Jesseforeman3825 I’m closing this issue since it’s resolved. Thanks again for your gift, I still can’t believe it. Don’t hesitate to open new issues if you have any questions. I hope you’ll make a fork of the project and that we’ll soon be able to see your creations.

Jesseforeman3825, 2024-04-15:
Thank you so much for the help. I was stuck. I’ll be sure to reach out if I
have questions. When I get further along on the project I’ll totally share
it with you guys.

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

NicHub, 2024-04-20:
@Jesseforeman3825, you might be interested in this issue :

https://github.com/NicHub/stewart-platform-esp32/issues/4

Closed 2024-04-15.

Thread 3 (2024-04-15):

loading Gcode

VeridisQuo555, 2024-04-15:
I was just wonder what your method of loading gcode

NicHub, 2024-04-15:
Currently, the program accepts G-code sent one command after another via the serial port. To send these commands, you can use any software that communicates over the serial port. In this project, I’ve chosen to write a Python script that reads a text file containing the gcode instructions and sends them one by one to the platform.

To use it, you need to upload the project on the ESP with this setting in platformio.ini: ’ENABLE_SERIAL_READ=true’.

Then on your computer, open a terminal, go to the gcode2serial directory and execute the Python program that sends the G-code commands to the platform. You’ll need to change <SERIAL PORT> with the ESP32 serial port, i.e. something like COMx, where x is a number.

```
cd <gcode2serial>
py gcode2serial.py -p <SERIAL PORT> -f demo_123.gcode
```

NicHub, 2024-04-15:
If you want to operate the platform in real time from a computer, you have to send the command in G-code format one by one.

But you can also hardcode the commands in the ESP. There are some examples in `Hexapod_Demo.cpp`:

- `demoMov_circles`
- `demoMov_shakeHeave`
- `demoMov_MinMaxAllAxis`

VeridisQuo555, 2024-04-15:
i see ill try it out

NicHub, 2024-04-20:
@VeridisQuo555, you might be interested in this issue :

https://github.com/NicHub/stewart-platform-esp32/issues/4

Closed 2024-06-09.

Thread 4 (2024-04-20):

Changed ATT pin cabling from IO35 to IO32.

NicHub, 2024-04-20:
Initially, the ATT pin which detects the Nunchuck connection was connected to IO35. This is a bad idea because this IO can only be configured as INPUT and not as INPUT_PULLDOWN as it should be. So I changed the wiring so that IO32 is used instead.

See https://github.com/NicHub/stewart-platform-esp32/commit/4fb5ff817b43e2fc8f8dd388226081e027dbc8ab

For reference, the pins that cannot or should not be used can be seen here:
https://ouilogique.com/files/2015-05-28-pinouts/images/esp32-wroom-32-pinout.png

Closed 2024-05-26.

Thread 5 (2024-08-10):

Algorithm 3 Derivation / Explanation?

jfrabosi, 2024-08-10:
Hi,

I've been working on modifying this repository to control four hexapod platforms at once, and I've been trying to understand how the inverse kinematics algorithms work. I've been looking at the source code but am struggling to find how Algorithm 3 is derived. Do you have any source documents that explain it? I've tried to derive it myself using the law of cosines and other trigonometry identities, but am struggling to get it to match your Algorithm 3.

double i1 = -ARM_LENGTH4 - ROD_LENGTH4 - a4 - b4 - c4
                     + 2 * (ARM_LENGTH2 * (ROD_LENGTH2 + a2 - b2 + c2)
                     + ROD_LENGTH2 * a2 + ROD_LENGTH2 * (b2 + c2)
                      - a2 * (b2 + c2) - b2 * c2);
        if (i1 < 0)
        {
            movOK = -5;
            break;
        }
        i1 = sqrt(i1);
        i1 = (2 * ARM_LENGTH * c - i1) /
             (ARM_LENGTH2 + 2 * ARM_LENGTH * a -
              ROD_LENGTH2 + BP2);
        i1 = 2 * atan(i1); // ~10 µs
        new_servo_angles[sid].rad = i1;

Any help is greatly appreciated!

Jakob

jfrabosi, 2024-08-10:
I figured it out. For anyone in the future who reads this, here's how Algorithm 3 works:

First, write out these two equations. They relate the servo arm BA and the rod arm AP, as defined in the stewart-platform-esp32/doc/hexapod-parameters.png image.

(x-a)^2 + b^2 + (z-c)^2 = L^2
x^2 + z^2 = R^2

where:
point B is located at (0, 0, 0)
A is located at (x, 0, z) (servo arm can only rotate in XZ plane)
P is located at (a, b, c)
the servo arm has length L
the rod arm has length R

Then, expand the first equation and substitute in the second equation for the x^2 + z^2 term to get our third equation.

We can draw a triangle with adjacent side x, opposite side z, hypotenuse L, and closest angle theta. We want to solve theta to determine what the angle of the servo should be. From this triangle, we get:

tan(theta) = x / z

We'll be working with the half angle tangent identities, so we'll create a variable t to help us out.

t = tan(theta/2) = x/2z

Use the following trig identities:

sin(theta) = 2t / (1+t^2)
cos(theta) = (1 - t^2) / (1 + t^2)

Then, substitute these identities for x and z:

x = L*cos(theta) = L * (1 - t^2) / (1 + t^2)
z = L*sin(theta) = L *  2t / (1+t^2)

Substitute these for x and z into the third equation from further above. Expand all of the terms and get it in the form below:

A*t^2 + B*t + c = 0

then use the quadratic formula, using the minus half of the plus/minus sign:

t = (-B - sqrt(B^2 - 4*A*C)) / 2A

Going back to the code now, the first line double i1 = ... is everything inside the square root term. So, for the first line,

i1 = B^2 - 4*A*C

if you expand the terms, you'll see that they all match up. Technically, you should expand all the terms first since the 2 in the denominator does some work inside the square root, canceling some 2s, so do that first. If this term is negative, there's no solution.

Finally, we put that i1 term into the quadratic formula equation after taking its square root, so the next i1 line becomes:

i1 = (-B - i1) / 2A

Then, since we said t = tan(theta/2), we can easily solve for theta.

Sorry for the long-winded explanation. Hopefully this helps someone in the future!

NicHub, 2024-08-10:
Nice job, thank you for sharing!

Don’t hesitate to share also about your “four-hexapod-platform”. That will be awesome to see.

Note that I’ve updated the drawing as I replaced DraftSight with QCAD: https://github.com/NicHub/stewart-platform-esp32/commit/a8fb83896f55a8a61497d60b149bddcd26786423

NicHub, 2024-08-10:
Nice job, thank you for sharing.

Don’t hesitate to share also about your “four-hexapod-platform”. That will be awesome to see.

Note that I’ve updated the drawing as I replaced DraftSight with QCAD: https://github.com/NicHub/stewart-platform-esp32/commit/a8fb83896f55a8a61497d60b149bddcd26786423

jfrabosi, 2024-08-10:
It's actually part of my Master's thesis - I've included a picture below. Thank you so much for making this project open-source - my project wouldn't be possible without your work! You're properly credited throughout the thesis and my code, of course.
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

NicHub, 2024-08-10:
It looks so cool! Do you have a video of it? What's the subject of your Master's thesis?

jfrabosi, 2024-08-10:
Thank you! Yes, here's one showing the full range-of-motion about the roll and pitch axes.
https://www.youtube.com/shorts/3j4FkxVK0gE

My Master's thesis subject is designing an acoustic positioning system for autonomous submarines. The windmill-looking attachment on the end effector is an acoustic array, with four ultrasonic microphones on it. I have a transmitter a set distance away, and I record an acoustic pulse on each of the receivers. Doing some signal processing and sensor fusion, I can get an estimate for where the acoustic array is relative to the transmitter. In the video below, you can see the audio signals shift in time when the hexapod changes position/orientation.
https://www.youtube.com/watch?v=QgJyHS0l2EE

The thesis is an above-water proof-of-concept. The hexapod bot is simulating the movements of a submarine. In the real version, the acoustic array would be fixed on a submarine and the transmitter would be on a buoy, projecting sound down towards the ocean floor / submarine. Above-water is easier to work with since nothing needs to be waterproofed and the speed of sound is 4.5x slower (however, sound propagates much less efficiently in air, so my range is quite limited!)

I'll be posting the code on my GitHub account soon - I'm almost done with writing the chapter about the hexapod positioner (which I call the Fo-SHIP, Four-Stacked Hexapod Isometric Platform, pronounced "faux-ship")

NicHub, 2024-08-11:
Exciting project! The videos are amazing. I’m curious to see your code.

I once worked for a manufacturer of ultrasonic car detection systems for parking lots. I know that it can be difficult to filter unwanted reflections and other pesky sources of errors.

By the way, why did you choose a “Four-Stacked Hexapod Isometric Platform” design? Wouldn’t a simple off-the-shelf robotic arm have done the job?

jfrabosi, 2024-08-11:
Thank you! I just finished the chapter on the hexapod, if you're curious I've attached it as a PDF.

[2 Ground-Truth Positioning System.pdf](https://github.com/user-attachments/files/16572974/2.Ground-Truth.Positioning.System.pdf)

Thankfully, I'm only considering pretty head-on transmissions - noise from the environment and reflections can cause issues, but they tend to get averaged out over time. I also implement a Kalman filter to help de-noise the system.

I went with the Fo-SHIP because I thought it was neat! I'd only seen one other stacked hexapod platform before (from some NASA research) and thought it might be interesting to give it a shot. I proposed my thesis to my committee, and so the budget for the thesis is out of my own pocket - designing my own actuator kept the costs down significantly! Overall, I think it cost around $300 to build, and it has an average positional accuracy of 7.35mm (better for smaller angles, worse for larger). Would definitely have preferred a pre-made actuator to get better accuracy, but it wasn't in the cards for me. Plus, I wanted to make something unique.

NicHub, 2024-08-21:
It seems to me that the text is correct, no problem.

However, in the references, there's a problem with the “é” character and the capital letters are missing.
The correct version is:

> [8] N. Jeanmonod, “Plateforme de Stewart pilotée avec un ESP32,”

And the link to reference [9] is broken.
The correct link is:

> https://github.com/NicHub/stewart-platform-esp32/

or if you want to specify which commit you based your work on (adapt the commit id accordingly:

> https://github.com/NicHub/stewart-platform-esp32/tree/4fb5ff817b43e2fc8f8dd388226081e027dbc8ab

NicHub, 2024-08-21:
By the way I am currently looking for a job and I would like to cite your work.

If you agree, can you tell me the title of your thesis, the name of the institution you are working with, and of course your name?

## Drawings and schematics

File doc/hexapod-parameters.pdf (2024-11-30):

x

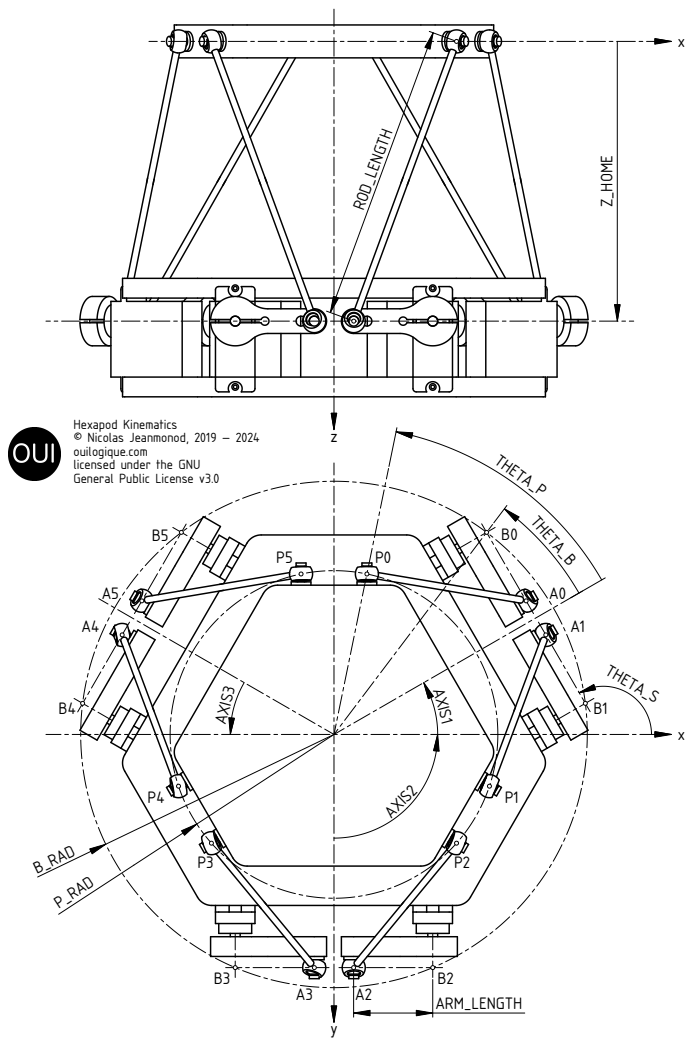
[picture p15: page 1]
ROD_LENGTH; ARM_LENGTH; B_RAD; THETA_B; THETA_P; THETA_S; AXIS3; AXIS1; AXIS2; P_RAD

Hexapod Kinematics
© Nicolas Jeanmonod, 2019 — 2024
ouilogique.com
licensed under the GNU
General Public License v3.0

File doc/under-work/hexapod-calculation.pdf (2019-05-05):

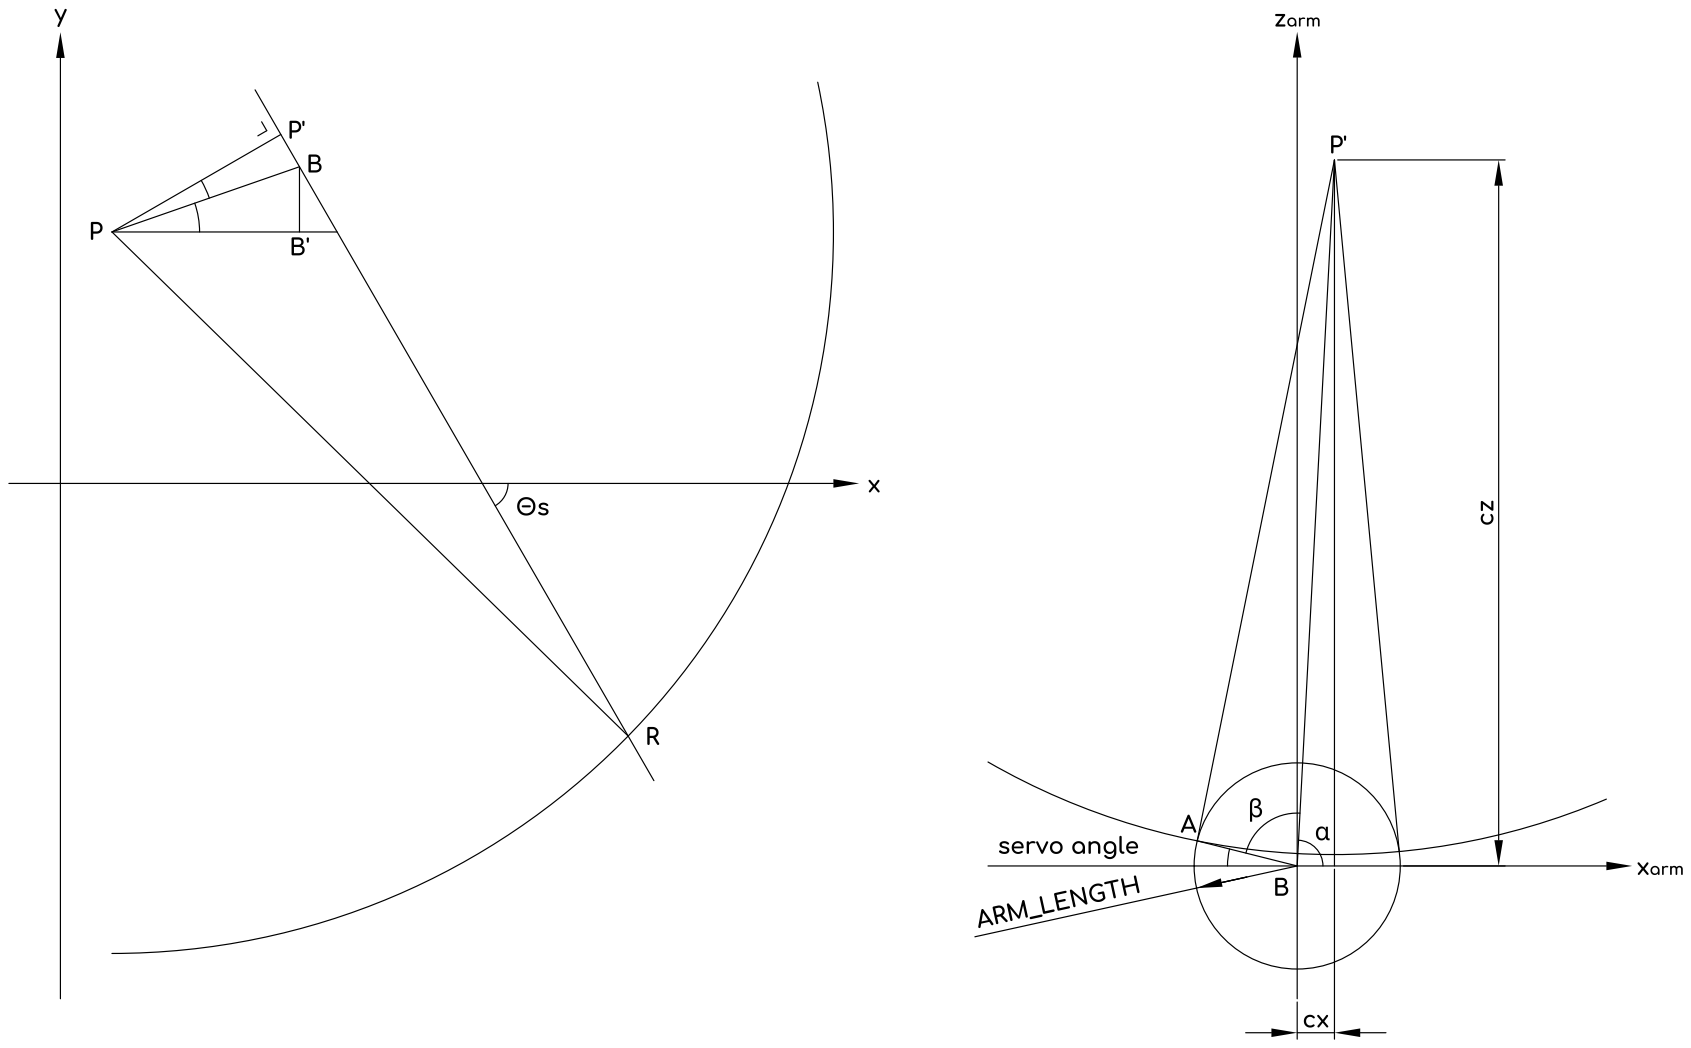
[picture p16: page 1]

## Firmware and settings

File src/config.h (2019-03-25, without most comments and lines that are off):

#include <Arduino.h>
#define __STU_CONFIG_H__
#define ENABLE_SERIAL_COMMANDS    //Comment out, to omit Command shell code.
#define LOG_LEVEL       Logger::DEBUG
const int SERVO_REVERSE[6] = {0, 0, 1, 0, 1, 0}; // Attention le premier moteur n’est pas du même type que les autres c’est pourquoi il est inversé.
#define SERVO_MIN_ANGLE     0
#define SERVO_MAX_ANGLE     100
const int SERVO_MID_ANGLE = SERVO_MIN_ANGLE + (SERVO_MAX_ANGLE - SERVO_MIN_ANGLE) / 2;
#define SERVO_MIN_US        800
#define SERVO_MAX_US        2000
const int SERVO_MID_US = SERVO_MIN_US + (SERVO_MAX_US - SERVO_MIN_US) / 2;
const int SERVO_TRIM[] = {  //trim values, in microseconds, AFTER reversing
  0,
  20,
  0,
  135,
  0,
  120
};
const int SERVO_PINS[] = {  //pin numbers for each servo signal.
  13,
  15,
  27,
  14,
  33,
  25
};
typedef struct xy_coordf {
  float x;  //-1.0 to 1.0
  float y;   //-1.0 to 1.0
} xy_coordf;
const xy_coordf DEFAULT_SETPOINT = {0,0};
#define MIN_PITCH  -20
#define MAX_PITCH  23
const int PITCH_BAND = MAX_PITCH - MIN_PITCH;
#define MIN_ROLL   -23
#define MAX_ROLL   20
const int ROLL_BAND = MAX_ROLL - MIN_ROLL;
#define MIN_YAW   -69
#define MAX_YAW   69
const int YAW_BAND = MAX_YAW - MIN_YAW;
#define MIN_SWAY   -55
#define MAX_SWAY   55
const int SWAY_BAND = MAX_SWAY - MIN_SWAY;
#define MIN_SURGE   -70
#define MAX_SURGE   55
const int SURGE_BAND = MAX_SURGE - MIN_SURGE;
#define MIN_HEAVE   -22
#define MAX_HEAVE   25
const int HEAVE_BAND = MAX_HEAVE - MIN_HEAVE;
#define THETA_P_DEG     45.25     //Platform joint angle (degrees) offset from AXIS[1|2|3]. A value of zero puts these joints directly on the axes
#define THETA_B_DEG     24.5      //Base Servo pinion angle (degrees) offset from AXIS[1|2|3]. A value of zero puts the servo pinion directly on the axes
#define THETA_P         (THETA_P_DEG * PI / 180)  //Theta P, in radians
#define THETA_B         (THETA_B_DEG * PI / 180)  //Theta B, in radians
#define P_RAD           50        //Platform radius (mm). The distance from the center of the platform to the center of one platform / pushrod "joint". This should be the same for all six pushrods.
#define B_RAD           80.2      //Base radius (mm). Distance from the center of the base plate to the center of one servo pinion gear. Again, this should be the same for all six servos.
#define ARM_LENGTH      25        //Servo arm length (mm). Distance from the center of the servo pivot to the center of the pushrod pivot on the servo arm.
#define ROD_LENGTH      155       //Push rod length (mm). Distance between pushrod ball joints (servo to platform).
#define Z_HOME          148       //Default Z height of the platform (above the base), with servo arms horizontal. Formally, the distance from the plane described by the collection of servo pinion gear centers, to the plane described by the collection of platform / pushrod joints.
#define AGGRO       1.5F
#define AXIS1       (PI / 6)  //30 degrees.
#define AXIS2       (-PI / 2) //-90 degrees.
#define AXIS3             AXIS1
const double THETA_S_DEG[6] = {
  -60,
  120,
  180,
  0,
  60,
  -120
};
const double THETA_S[6] = {     //Servo arm angle (radians)
  radians(THETA_S_DEG[0]),
  radians(THETA_S_DEG[1]),
  radians(THETA_S_DEG[2]),
  radians(THETA_S_DEG[3]),
  radians(THETA_S_DEG[4]),
  radians(THETA_S_DEG[5])
};
const double P_COORDS[6][2] = {
  {P_RAD * cos(AXIS1 + THETA_P), P_RAD * sin(AXIS1 + THETA_P)},
  {P_RAD * cos(AXIS1 - THETA_P), P_RAD * sin(AXIS1 - THETA_P)},
  {P_RAD * cos(AXIS2 + THETA_P), P_RAD * sin(AXIS2 + THETA_P)},
  { -P_RAD * cos(AXIS2 + THETA_P), P_RAD * sin(AXIS2 + THETA_P)},
  { -P_RAD * cos(AXIS3 - THETA_P), P_RAD * sin(AXIS3 - THETA_P)},
  { -P_RAD * cos(AXIS3 + THETA_P), P_RAD * sin(AXIS3 + THETA_P)}
};
const double B_COORDS[6][2] = {
  {B_RAD * cos(AXIS1 + THETA_B), B_RAD * sin(AXIS1 + THETA_B)},
  {B_RAD * cos(AXIS1 - THETA_B), B_RAD * sin(AXIS1 - THETA_B)},
  {B_RAD * cos(AXIS2 + THETA_B), B_RAD * sin(AXIS2 + THETA_B)},
  { -B_RAD * cos(AXIS2 + THETA_B), B_RAD * sin(AXIS2 + THETA_B)},
  { -B_RAD * cos(AXIS3 - THETA_B), B_RAD * sin(AXIS3 - THETA_B)},
  { -B_RAD * cos(AXIS3 + THETA_B), B_RAD * sin(AXIS3 + THETA_B)}
};

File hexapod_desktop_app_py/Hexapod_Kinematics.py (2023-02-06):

"""

S T E W A R T    P L A T F O R M    O N    E S P 3 2

Copyright (C) 2019  Nicolas Jeanmonod, ouilogique.com

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
##################

Works on
MicroPython v1.19.1 on 2022-06-18; ESP32 module with ESP32

Doesn’t work on
MicroPython v1.16-200-g1b87e1793 on 2021-08-12; LOLIN_S2_MINI with ESP32-S2FN4R2
(no f-string support)

| SYSTEM                       | TIME PER CALCULATION |
| ---------------------------- | -------------------: |
| MicroPython v1.19.1 on ESP32 |            ~ 4000 µs |
| C++ on ESP32                 |             ~ 250 µs |
| Python on Apple M1 Pro       |              ~ 12 µs |
| C++ on Apple M1 Pro          |               ~ 2 µs |

"""
HEXAPOD_CONFIG = 1
if HEXAPOD_CONFIG == 1:
    import Hexapod_Config_1 as hc
import math
import time

SMALL_WIDTH = 7
LARGE_WIDTH = 17
START_DATE = time.time()

CPU_TIME_USED = 0
COUNTER = 0


#
# ======== PRECALCULATED GEOMETRY ==========
#

#
# There are three axes of symmetry (AXIS1, AXIS2, AXIS3). Looking down on the
# platform from above (along the Y axis), with 0 degrees being the X-positive line, and traveling
# in a CC direction, these are at 30 degrees, 120 degrees, and 240 degrees. All
# the polar coordinates of pivot points, servo centers, etc. are calculated based on
# an axis, and an offset angle (positive or negative theta) from the axis.

# NOTE: We make an assumption of mirror symmetry for AXIS3 along the Y axis.
# That is, AXIS1 is at (e.g.) 30 degrees, and AXIS3 will be at 120 degrees
# We account for this by negating the value of x-coordinates generated based
# on this axis later on. This is potentially messy, and should maybe be refactored.
#
AXIS1 = math.pi / 6  # 30 degrees.
AXIS2 = -math.pi / 2  # -90 degrees.
AXIS3 = AXIS1


#
# Orientations of the servos arms relative to the X axis.
#
COS_THETA_S = (
    math.cos(hc.THETA_S[0]),
    math.cos(hc.THETA_S[1]),
    math.cos(hc.THETA_S[2]),
    math.cos(hc.THETA_S[3]),
    math.cos(hc.THETA_S[4]),
    math.cos(hc.THETA_S[5]),
)


SIN_THETA_S = (
    math.sin(hc.THETA_S[0]),
    math.sin(hc.THETA_S[1]),
    math.sin(hc.THETA_S[2]),
    math.sin(hc.THETA_S[3]),
    math.sin(hc.THETA_S[4]),
    math.sin(hc.THETA_S[5]),
)

# For algorithm 2
M_THETA_S = (
    -hc.THETA_S[0],
    -hc.THETA_S[1],
    -hc.THETA_S[2],
    -hc.THETA_S[3],
    -hc.THETA_S[4],
    -hc.THETA_S[5],
)

sinD = (
    math.sin(M_THETA_S[0]),
    math.sin(M_THETA_S[1]),
    math.sin(M_THETA_S[2]),
    math.sin(M_THETA_S[3]),
    math.sin(M_THETA_S[4]),
    math.sin(M_THETA_S[5]),
)

cosD = (
    math.cos(M_THETA_S[0]),
    math.cos(M_THETA_S[1]),
    math.cos(M_THETA_S[2]),
    math.cos(M_THETA_S[3]),
    math.cos(M_THETA_S[4]),
    math.cos(M_THETA_S[5]),
)

#
# XY cartesian coordinates of the platform joints, based on the polar
# coordinates (platform radius P_RAD, radial axis AXIS[1|2|3], and offset THETA_P.
# These coordinates are in the plane of the platform itself.
#
P_COORDS = (
    (hc.P_RAD * math.cos(AXIS1 + hc.THETA_P), hc.P_RAD * math.sin(AXIS1 + hc.THETA_P)),
    (hc.P_RAD * math.cos(AXIS1 - hc.THETA_P), hc.P_RAD * math.sin(AXIS1 - hc.THETA_P)),
    (hc.P_RAD * math.cos(AXIS2 + hc.THETA_P), hc.P_RAD * math.sin(AXIS2 + hc.THETA_P)),
    (-hc.P_RAD * math.cos(AXIS2 + hc.THETA_P), hc.P_RAD * math.sin(AXIS2 + hc.THETA_P)),
    (-hc.P_RAD * math.cos(AXIS3 - hc.THETA_P), hc.P_RAD * math.sin(AXIS3 - hc.THETA_P)),
    (-hc.P_RAD * math.cos(AXIS3 + hc.THETA_P), hc.P_RAD * math.sin(AXIS3 + hc.THETA_P)),
)

#
# XY cartesian coordinates of the servo centers, based on the polar
# coordinates (base radius B_RAD, radial axis AXIS[1|2|3], and offset THETA_B.
# These coordinates are in the plane of the base itself.
#
B_COORDS = (
    (hc.B_RAD * math.cos(AXIS1 + hc.THETA_B), hc.B_RAD * math.sin(AXIS1 + hc.THETA_B)),
    (hc.B_RAD * math.cos(AXIS1 - hc.THETA_B), hc.B_RAD * math.sin(AXIS1 - hc.THETA_B)),
    (hc.B_RAD * math.cos(AXIS2 + hc.THETA_B), hc.B_RAD * math.sin(AXIS2 + hc.THETA_B)),
    (-hc.B_RAD * math.cos(AXIS2 + hc.THETA_B), hc.B_RAD * math.sin(AXIS2 + hc.THETA_B)),
    (-hc.B_RAD * math.cos(AXIS3 - hc.THETA_B), hc.B_RAD * math.sin(AXIS3 - hc.THETA_B)),
    (-hc.B_RAD * math.cos(AXIS3 + hc.THETA_B), hc.B_RAD * math.sin(AXIS3 + hc.THETA_B)),
)

#
# Square of the longest physically possible distance
# between servo pivot and platform joint.
#
BP2_MAX = (hc.ARM_LENGTH + hc.ROD_LENGTH) ** 2

#
# ARM^2, ARM^4, ROD^2, ROD^4,
#
ARM_LENGTH2 = hc.ARM_LENGTH**2
ARM_LENGTH4 = hc.ARM_LENGTH**4
ROD_LENGTH2 = hc.ROD_LENGTH**2
ROD_LENGTH4 = hc.ROD_LENGTH**4

#
# Square of the length of BP when the servo arm is perpendicular to BP.
#
BP2_PERP = ROD_LENGTH2 - ARM_LENGTH2


class Hexapod_Kinematics:
    """___"""

    def __init__(self):
        """___"""
        pass

    def mapDouble(self, x, in_min, in_max, out_min, out_max):
        """___"""
        return (x - in_min) * (out_max - out_min) / (in_max - in_min) + out_min

    def calcServoAngles(self, coord):
        """
        Calculation of the servo angles in radians, degrees and in microseconds (PWM)
        given the desired target platform coordinates.

        @param coord : the desired target platform coordinates.
        A struct containing X (surge), Y (sway), Z (heave) in mm
        and A (roll), B (pitch) and C (yaw) in radians.

        @param servo_angles : pointer to an array of struct containing
        the calculated servos angles in radians, degrees and in microseconds (PWM).

        @return
        Returns = 0 if OK
        Returns < 0 if Error
        """
        movOK = 0
        if hc.ALGO == 1:
            movOK, servo_angles = self.calcServoAnglesAlgo1(coord)
        elif hc.ALGO == 2:
            movOK, servo_angles = self.calcServoAnglesAlgo2(coord)
        elif hc.ALGO == 3:
            movOK, servo_angles = self.calcServoAnglesAlgo3(coord)

        return movOK, servo_angles

    def home(self):
        """
        HOME position. No translation, no rotation.
        """
        movOK, servo_angles = self.calcServoAngles(
            {"hx_x": 0, "hx_y": 0, "hx_z": 0, "hx_a": 0, "hx_b": 0, "hx_c": 0}
        )
        return movOK, servo_angles

    def calcServoAnglesAlgo3(self, coord):
        """___"""
        # Number of time the function was called.
        # nb_call = 0
        # ++nb_call;

        null_servo_angles = (
            {"rad": 0, "deg": 0, "pwm": 0, "pwm_us": 0},
            {"rad": 0, "deg": 0, "pwm": 0, "pwm_us": 0},
            {"rad": 0, "deg": 0, "pwm": 0, "pwm_us": 0},
            {"rad": 0, "deg": 0, "pwm": 0, "pwm_us": 0},
            {"rad": 0, "deg": 0, "pwm": 0, "pwm_us": 0},
            {"rad": 0, "deg": 0, "pwm": 0, "pwm_us": 0},
        )
        new_servo_angles = null_servo_angles

        # Intermediate values, to avoid recalculating sin math cos.
        # (3 µs).
        cosA = math.cos(coord["hx_a"])
        cosB = math.cos(coord["hx_b"])
        cosC = math.cos(coord["hx_c"])
        sinA = math.sin(coord["hx_a"])
        sinB = math.sin(coord["hx_b"])
        sinC = math.sin(coord["hx_c"])

        # Assume everything will be OK.
        movOK = 0
        for sid in range(hc.NB_SERVOS):
            # Compute the new platform joint coordinates relative to servo pivot.
            # (~7 µs)
            BP_x = (
                P_COORDS[sid][0] * cosB * cosC
                + P_COORDS[sid][1] * (sinA * sinB * cosC - cosA * sinC)
                + coord["hx_x"]
                - B_COORDS[sid][0]
            )
            BP_y = (
                P_COORDS[sid][0] * cosB * sinC
                + P_COORDS[sid][1] * (sinA * sinB * sinC + cosA * cosC)
                + coord["hx_y"]
                - B_COORDS[sid][1]
            )
            BP_z = (
                -P_COORDS[sid][0] * sinB
                + P_COORDS[sid][1] * sinA * cosB
                + coord["hx_z"]
                - hc.Z_HOME
            )

            # print(f"{BP_x:20.1f}")
            # print(f"{cosA:20.5f}")
            # print(f'{coord["hx_a"]:20.5f}')

            a = COS_THETA_S[sid] * BP_x + SIN_THETA_S[sid] * BP_y
            b = -SIN_THETA_S[sid] * BP_x + COS_THETA_S[sid] * BP_y
            c = BP_z
            a2 = a**2
            a4 = a**4
            b2 = b**2
            b4 = b**4
            c2 = c**2
            c4 = c**4

            # Distance^2 between servo pivot (B) and platform joint (P).
            # Note that BP_x^2 + BP_y^2 + BP_z^2 = a^2 + b^2 + c^2, so
            # we can compare BP2 to BP2_MAX in the next test.
            BP2 = a2 + b2 + c2

            # Test if the new distance between servo pivot and platform joint
            # is longer than physically possible.
            # Abort computation of remaining angles if the current angle is not OK.
            # (~1 µs)
            if BP2 > BP2_MAX:
                movOK = -1
                break

            i1 = (
                -ARM_LENGTH4
                - ROD_LENGTH4
                - a4
                - b4
                - c4
                + 2
                * (
                    ARM_LENGTH2 * (ROD_LENGTH2 + a2 - b2 + c2)
                    + ROD_LENGTH2 * a2
                    + ROD_LENGTH2 * (b2 + c2)
                    - a2 * (b2 + c2)
                    - b2 * c2
                )
            )
            if i1 < 0:
                movOK = -5
                break
            i1 = math.sqrt(i1)
            i1 = (2 * hc.ARM_LENGTH * c - i1) / (
                ARM_LENGTH2 + 2 * hc.ARM_LENGTH * a - ROD_LENGTH2 + BP2
            )
            i1 = 2 * math.atan(i1)
            new_servo_angles[sid]["rad"] = i1

            # Rotate the angle.
            # (~1 µs)
            new_servo_angles[sid]["rad"] += hc.SERVO_HALF_ANGULAR_RANGE

            # Convert radians to degrees.
            # (~2 µs)
            new_servo_angles[sid]["deg"] = math.degrees(new_servo_angles[sid]["rad"])

            # print(new_servo_angles[sid]["rad"])
            # print(hc.SERVO_CALIBRATION)
            # print(hc.SERVO_CALIBRATION[sid]["gain"])
            # return -1, null_servo_angles

            # Convert radians to PWM.
            # The calibration values take into account the fact
            # that the odd and even arms are a reflection of each other.
            # (~5 µs)
            new_servo_angles[sid]["pwm_us"] = (
                round(hc.SERVO_CALIBRATION[sid]["gain"] * new_servo_angles[sid]["rad"])
                + hc.SERVO_CALIBRATION[sid]["offset"]
            )

            # Check if the angle is in min/max.
            # Abort computation of remaining angles if the current angle is not OK.
            # (~1 µs)
            if new_servo_angles[sid]["pwm_us"] > hc.SERVO_MAX_PWM:
                movOK = -3
                break
            elif new_servo_angles[sid]["pwm_us"] < hc.SERVO_MIN_PWM:
                movOK = -4
                break

        # Update platform coordinates if there are no errors.
        # (~1 µs)
        if movOK != 0:
            new_servo_angles = null_servo_angles
        return movOK, new_servo_angles


def calcAndPrintResults(
    hk, coord={"hx_x": 0, "hx_y": 0, "hx_z": 0, "hx_a": 0, "hx_b": 0, "hx_c": 0}
):
    """___"""

    try:
        t1 = time.ticks_us()
    except AttributeError:
        t1 = time.time() * 1e6
    movOK, angles = hk.calcServoAngles(coord)
    try:
        t2 = time.ticks_us()
    except AttributeError:
        t2 = time.time() * 1e6

    global CPU_TIME_USED
    global COUNTER
    CPU_TIME_USED += t2 - t1
    COUNTER += 1

    ans = f'{coord["hx_x"]:{SMALL_WIDTH}.1f}'
    ans += f'{coord["hx_y"]:{SMALL_WIDTH}.1f}'
    ans += f'{coord["hx_z"]:{SMALL_WIDTH}.1f}'
    ans += f'{math.degrees(coord["hx_a"]):{SMALL_WIDTH}.1f}'
    ans += f'{math.degrees(coord["hx_b"]):{SMALL_WIDTH}.1f}'
    ans += f'{math.degrees(coord["hx_c"]):{SMALL_WIDTH}.1f}'
    ans += f"{movOK:{SMALL_WIDTH}}"

    if movOK == 0:
        ans += f'{angles[0]["pwm_us"]:{LARGE_WIDTH}.0f}'
        ans += f'{angles[1]["pwm_us"]:{LARGE_WIDTH}.0f}'
        ans += f'{angles[2]["pwm_us"]:{LARGE_WIDTH}.0f}'
        ans += f'{angles[3]["pwm_us"]:{LARGE_WIDTH}.0f}'
        ans += f'{angles[4]["pwm_us"]:{LARGE_WIDTH}.0f}'
        ans += f'{angles[5]["pwm_us"]:{LARGE_WIDTH}.0f}'

    ans += "\n"
    return ans


if __name__ == "__main__":

    hk = Hexapod_Kinematics()
    ans = hk.home()
    # pprint(ans)
    # pprint(hc.HX_Y_MIN)
    shrink = 3
    nb_intervals = 1

    HX_Xs = [-8, 8]
    HX_Ys = [-8, 8]
    HX_Zs = [-4, 4]
    HX_As = [math.radians(-12) / shrink, math.radians(12) / shrink]
    HX_Bs = [math.radians(-12) / shrink, math.radians(12) / shrink]
    HX_Cs = [math.radians(-43) / shrink, math.radians(43) / shrink]

    ans = ""
    ans += "      X      Y      Z      A      B      C  movOK          ANGLE 1          ANGLE 2          ANGLE 3          ANGLE 4          ANGLE 5          ANGLE 6\n"
    ans += "=======================================================================================================================================================\n"

    ans += calcAndPrintResults(
        hk, {"hx_x": 0, "hx_y": 0, "hx_z": 0, "hx_a": 0, "hx_b": 0, "hx_c": 0}
    )
    ans += calcAndPrintResults(
        hk, {"hx_x": 0, "hx_y": 0, "hx_z": hc.HX_Z_MAX, "hx_a": 0, "hx_b": 0, "hx_c": 0}
    )
    ans += calcAndPrintResults(
        hk, {"hx_x": 0, "hx_y": 0, "hx_z": hc.HX_Z_MIN, "hx_a": 0, "hx_b": 0, "hx_c": 0}
    )
    ans += "=======================================================================================================================================================\n"
    for hx_x in HX_Xs:
        for hx_y in HX_Ys:
            for hx_z in HX_Zs:
                for hx_a in HX_As:
                    for hx_b in HX_Bs:
                        for hx_c in HX_Cs:
                            coord = {
                                "hx_x": hx_x,
                                "hx_y": hx_y,
                                "hx_z": hx_z,
                                "hx_a": hx_a,
                                "hx_b": hx_b,
                                "hx_c": hx_c,
                            }
                            ans += calcAndPrintResults(hk, coord)

    ans += "\n\nSTEWART PLATFORM\n"
    # ans += "COMPILATION DATE AND TIME\n"
    # ans += f"{START_DATE}\n"
    # ans += f"{time.time()}\n"
    # ans += '{START_DATE.strftime("%H:%M:%S")}\n'
    ans += f"HEXAPOD_CONFIG            : {HEXAPOD_CONFIG}\n"
    ans += f"ALGORITHM                 : {hc.ALGO}\n"
    ans += f"LANGAGE                   : Python\n"
    ans += f"Total time elapsed   (µs) : {CPU_TIME_USED:0.1f}\n"
    ans += f"Time per calculation (µs) : {CPU_TIME_USED / COUNTER:0.2f}\n"
    ans += f"Calculation count         : {COUNTER}\n"
    ans += "\n"
    print(ans)

    filename = f"angles_with_config_{HEXAPOD_CONFIG}_py.txt"
    with open(file=filename, mode="wt", encoding="utf-8") as _f:
        _f.write(ans)

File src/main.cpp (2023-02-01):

/**
 * S T E W A R T    P L A T F O R M    O N    E S P 3 2
 *
 * Copyright (C) 2019  Nicolas Jeanmonod, ouilogique.com
 *
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
 */

// External libs.
#include <Arduino.h>
#include <PCA9685.h>
#include <WiiChuck.h>

// Hexapod libs.
#include <Hexapod_Demo.h>
#include <Hexapod_GPIO.h>
#include <Hexapod_Nunchuck.h>
#include <Hexapod_Kinematics.h>
#include <Hexapod_Serial.h>
#include <Hexapod_Servo.h>
#include <Hexapod_imu.h>
#include <Hexapod_WebServerApp.h>

AsyncWebSocket ws("/ws");
AsyncWebServer server(80);
AsyncEventSource events("/events");

IMU imu1;

const unsigned short fifoRate = 20U; // IMU refresh rate in Hz.

// Global variables.
angle_t servo_angles[NB_SERVOS];
Hexapod_Servo hx_servo; // Servo pins are defined in Hexapod_Config_`x`.h (where `x` is the file number)
Hexapod_Serial hx_serial;
Hexapod_Nunchuck hx_nunchuck;
Hexapod_Demo hx_demo;
Hexapod_GPIO hx_gpio;

/**
 *
 */
void setup()
{
    // Setup.
    hx_gpio.setupGPIO();
    hx_serial.setupSerial();
    hx_serial.printSplashScreen();
    hx_servo.setupServo();

#if ENABLE_NUNCHUCK_READ
    hx_nunchuck.setupNunchuck();
#endif

#if ENABLE_IMU_READ
    scanNetwork();
    setupWebServer();
    imu1.setupIMU(fifoRate);
#endif

    hx_demo.demoMov_circles(DEMO_CIRCLES_NB_TURN);

    // Go to home position.
    uint8_t movOK = hx_servo.calcServoAngles({0, 0, 0, 0, 0, 0}, servo_angles);
    hx_servo.updateServos(movOK);

    // Find min and max coord.
    hx_demo.findMinMax();

    // Test calculation speed.
    hx_demo.testCalcSpeed();

#if false
    // Test calculations.
    hx_demo.testCalculations();
#endif
}

/**
 *
 */
void loop()
{
digitalWrite(DEBUG_PIN_1, LOW);
digitalWrite(DEBUG_PIN_1, HIGH);

#if ENABLE_NUNCHUCK_READ
    hx_nunchuck.stopIfNotConnected();
    hx_nunchuck.nunchuckControl();
#endif

#if ENABLE_SERIAL_READ
    hx_serial.serialRead();
#endif

#if ENABLE_IMU_READ
    static unsigned long T1 = millis();
    if ((millis() - T1) < (1000 / fifoRate))
        return;
    T1 = millis();

    ArduinoOTA.handle();

    if (!ws.enabled())
    {
        Serial.println("NO WebSocket!");
        return;
    }

    // Read IMU.
    static unsigned short status;
    static char jsonMsg[200];
    status = imu1.readIMU(jsonMsg);
    ws.textAll(jsonMsg);
    if (status != 0)
        Serial.println(jsonMsg);

    euler_angles_t eulerAngles = imu1.getEulerAngles();
    euler_angles_t angles = {
        (eulerAngles.eA - 180) * DEG_TO_RAD,
        (eulerAngles.eB - 360) * DEG_TO_RAD,
        (eulerAngles.eC - 120) * DEG_TO_RAD,
    };
    Serial.print(angles.eA);
    Serial.print(" ");
    Serial.print(angles.eB);
    Serial.print(" ");
    Serial.print(angles.eC);
    Serial.print("\n");

    // X, Y, tilt X, tilt Y
    int8_t movOK = hx_servo.calcServoAngles({0, 0, 0, angles.eA, angles.eB, angles.eC},
                                            servo_angles);
    hx_servo.updateServos(movOK);
#endif
}

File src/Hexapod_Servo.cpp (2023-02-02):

/**
 * S T E W A R T    P L A T F O R M    O N    E S P 3 2
 *
 * Copyright (C) 2019  Nicolas Jeanmonod, ouilogique.com
 *
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
 */

#include <Hexapod_Servo.h>
#include <Hexapod_GPIO.h>

#define COUNT_OF(x) ((sizeof(x) / sizeof(0 [x])) / ((size_t)(!(sizeof(x) % sizeof(0 [x])))))

extern angle_t servo_angles[NB_SERVOS];
extern Hexapod_GPIO hx_gpio;

/**
 *
 */
Hexapod_Servo::Hexapod_Servo()
{
}

/**
 *
 */
void Hexapod_Servo::setupServo()
{
    Wire.begin();          // Wire must be started first
    Wire.setClock(100000); // Supported baud rates are 100kHz, 400kHz, and 1000kHz

    pwmController.resetDevices();      // Software resets all PCA9685 devices on Wire line
    pwmController.init(B000001);       // Address pins A5-A0 set to B000000
    pwmController.setPWMFrequency(50); // Default is 200Hz, supports 24Hz to 1526Hz

    int8_t movOK = home(servo_angles);
    this->updateServos(movOK);
    delay(500);
}

/**
 * Set servo values to the angles in servo_angles[].
 */
void Hexapod_Servo::updateServosIncremental(int8_t movOK, unsigned long safetyWait_ms)
{
#if false
    static bool first_run = true;

    static angle_t _servo_angles_prev[NB_SERVOS];
    if (first_run)
    {
        for (uint8_t sid = 0; sid < NB_SERVOS; sid++)
        {
            _servo_angles_prev[sid].us = servo_angles[sid].us;
        }
        first_run = false;
        return;
    }

    static angle_t _servo_angles_target[NB_SERVOS];
    for (uint8_t sid = 0; sid < NB_SERVOS; sid++)
    {
        _servo_angles_target[sid].us = servo_angles[sid].us;
    }
    const int increment = 5;
    int8_t moving = B00111111;
    Serial.println("### MOVING START ");

    Serial.println("### ANGLE PREV ");
    for (uint8_t sid = 0; sid < NB_SERVOS; sid++)
    {
        Serial.printf("%4d ", _servo_angles_prev[sid].us);
    }
    Serial.println("\n### ANGLE TARGET ");
    for (uint8_t sid = 0; sid < NB_SERVOS; sid++)
    {
        Serial.printf("%4d ", _servo_angles_target[sid].us);
    }
    Serial.println("");

    while (moving)
    {
        for (uint8_t sid = 0; sid < NB_SERVOS; sid++)
        {
            double err = _servo_angles_target[sid].us - _servo_angles_prev[sid].us;

            if (err >= increment)
                _servo_angles_prev[sid].us += increment;
            else if (err <= -increment)
                _servo_angles_prev[sid].us -= increment;
            else
            {
                _servo_angles_prev[sid].us = _servo_angles_target[sid].us;
                bitClear(moving, sid);
            }

            Serial.printf("%4d ", _servo_angles_prev[sid].us);
        }
        // Write to servos.
        for (uint8_t sid = 0; sid < NB_SERVOS; sid++)
        {
            servos[sid].writeMicroseconds(_servo_angles_prev[sid].us);
        }

        delay(5);

        Serial.print("\n");
    }

    Serial.println(" MOVING DONE ###");
#endif
}

/**
 * Set servo values to the angles in servo_angles[].
 */
void Hexapod_Servo::updateServos(int8_t movOK, unsigned long safetyWait_ms)
{
    // Statistics of errors.
    static double nbMov = 0;
    static double nbMovNOK = 0;
    static double NOKrate = 0;
    nbMov++;

    if (movOK == 0)
    {
        // Do not update too quickly. This helps a little to prevent
        // the servos from going crazy. safetyWait_ms must be set to 0
        // when going on a smooth trajectory with a lot of points.
        static unsigned long T1;
        while ((millis() - T1) < safetyWait_ms)
        {
        }
        T1 = millis();

        // Write to servos.
        static uint16_t pwms[NB_SERVOS];
        for (uint8_t sid = 0; sid < NB_SERVOS; sid++)
        {
            pwms[sid] = servo_angles[sid].pwm_us;
        }
        pwmController.setChannelsPWM(0, NB_SERVOS, pwms);

#if SEND_PWM_US_TO_SERIAL
        // Write servo angles to Serial for debug.
        for (uint8_t sid = 0; sid < NB_SERVOS; sid++)
        {
            Serial.printf("%4d ", servo_angles[sid].pwm_us);
        }
        Serial.println("");
#endif
    }
    else
    {
        // Error handling.
        hx_gpio.setBuiltInLED();
        nbMovNOK++;
        NOKrate = (nbMovNOK / nbMov) * (double)100.0;
        Serial.printf("%10lu", millis());
        Serial.printf(" | BAD MOVE | movOK = %d", movOK);
        Serial.printf(" | NB MOV = %10.0f", nbMov);
        Serial.printf(" | NOK rate = %4.1f %%", NOKrate);
        Serial.print("\n");
    }

    // Switch off LED.
    hx_gpio.clearBuiltInLEDDelayed(20);
}

/**
 *
 */
void Hexapod_Servo::printServoAngles()
{
    Serial.print("\nSERVO COORD        = ");
    Serial.print(getHX_X());
    Serial.print(" ");
    Serial.print(getHX_Y());
    Serial.print(" ");
    Serial.print(getHX_Z());
    Serial.print(" ");
    Serial.print(getHX_A());
    Serial.print(" ");
    Serial.print(getHX_B());
    Serial.print(" ");
    Serial.print(getHX_C());

    Serial.print("\nSERVO_ANGLES (rad) = ");
    for (uint8_t sid = 0; sid < NB_SERVOS; sid++)
    {
        Serial.print(servo_angles[sid].deg);
        Serial.print(" ");
    }

    Serial.print("\nSERVO_ANGLES (us) = ");
    for (uint8_t sid = 0; sid < NB_SERVOS; sid++)
    {
        Serial.print(servo_angles[sid].us);
        Serial.print(" ");
    }

    Serial.print("\nSERVO_ANGLES (debug) = ");
    for (uint8_t sid = 0; sid < NB_SERVOS; sid++)
    {
        Serial.print(servo_angles[sid].debug);
        Serial.print(" ");
    }
    Serial.print("\n");
}

/**
 *
 */
void Hexapod_Servo::printJointAndServoAxisCoord()
{
    Serial.println("P_COORDS");
    for (uint8_t sid = 0; sid < NB_SERVOS; sid++)
    {
        Serial.print(P_COORDS[sid][0]);
        Serial.print("  ");
        Serial.println(P_COORDS[sid][1]);
    }

    Serial.println("\nB_COORDS");
    for (uint8_t sid = 0; sid < NB_SERVOS; sid++)
    {
        Serial.print(B_COORDS[sid][0]);
        Serial.print("  ");
        Serial.println(B_COORDS[sid][1]);
    }
}

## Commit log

2019-03-26 1ere implementation webserver -> bug joystick
    [HexapodKinematics.cpp, HexapodKinematics.h, main.cpp]
2019-03-27 calib joystick + testé avec fils de fer -> OK
2019-03-28 Init des servos avec SERVO_MIN_US, SERVO_MAX_US explicites.
2019-04-08 première implémentation de la lecture via Serial
2019-04-13 Limitation des mouvements
2019-04-13 séparation des configs
2019-04-13 code cleanup
    [joints_coord_config_1.txt]
2019-04-14 struct pour les valeurs des servos
2019-04-14 plateforme coord dans un struct
2019-04-14 corrigé bug joyMode + code cleanup
    [HexapodKinematics.cpp, main.cpp]
2019-04-16 modif Z_HOME pour que les bras soient horizontaux à l’origine
    [angles_config_1.txt, angles_config_2.txt, angles_config_3.txt]
2019-04-17 optimisation calculs + Z HOME
    [angles_config_1.txt, angles_config_2.txt, calc_zhome.ods]
2019-04-18 modif noms Hexapod => Hexapod_
    [angles_config_1.txt]
2019-04-18 renommé servo_t => angle_t
2019-04-18 speed test
    [angles_config_1.txt]
2019-04-19 optimisation du code
    [angles_config_1.txt, angles_config_2.txt]
2019-04-19 Nouvelle limites pour pitch et roll
    [angles_config_2.txt]
2019-04-20 renommé Hexapod_KinematicsConfig => Hexapod_Config
    [angles_config_1.txt, angles_config_2.txt]
2019-04-20 pas de mouvements si movOK != 0
    [angles_config_1.txt, angles_config_2.txt]
2019-04-21 ajout de safetyWait_ms
2019-04-22 réorganisation des includes et modif des en-têtes
    [angles_config_2.txt]
2019-04-22 Montage avec les servos digitaux
2019-04-24 augmenté nbJoyMode de 3 à 4
2019-04-26 changement des noms des variables de coordonnées
    [angles_config_1.txt, angles_config_2.txt, angles_config_3.txt]
2019-04-27 renommé variables et find min/max coord (print only)
2019-04-27 AGGRO = 1
    [angles_config_3.txt]
2019-04-27 param OK
    [angles_config_3.txt]
2019-04-27 optimisation de Z_HOME
    [angles_config_3.txt, calc_zhome.ods]
2019-04-28 Modif conversion rad -> pw
    [angles_config_1.txt]
2019-04-29 Ajustements des paramètres + schéma explicatif
    [angles_config_1.txt, angles_config_2.txt, angles_config_3.txt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]
2019-04-29 ajout THETA_S sur schéma et inclu THETA_S dans config individuelle
    [angles_config_1.txt, hexapod_parameters.dwg, joints_coord_config_1.txt]
2019-05-01 Avant correction algorithme
    [angles_config_1.txt]
2019-05-01 Après correction algorithme
    [angles_config_1.txt]
2019-05-01 doc kinematics
2019-05-01 Enlevé variable intermédiaire pas utile.
    [angles_config_1.txt]
2019-05-04 corrigé points B et rayon B_RAD
    [calc_zhome.ods, hexapod-parameters-v2.dwg, hexapod-parameters.dwg]
2019-05-04 modifs limites + PDF param généré par DraftSight
    [angles_config_1.txt, hexapod-parameters.dwg]
2019-05-04 textes PDF comme géométrie
    [hexapod-parameters.dwg]
2019-05-04 corrigé style ligne
    [hexapod-parameters.dwg]
2019-05-04 Théorie cinématique
    [calc_zhome.ods, hexapod-parameters.dwg]
2019-05-05 ajout licence
    [hexapod-parameters-v2.dwg, hexapod-parameters.dwg]
2019-05-19 Nouvel algorithme fonctionnel
    [angles_config_1.txt]
2019-05-30 Repris ancien algorithme pour trouver bug
    [angles_config_2.txt]
2019-05-31 debug pbm servo avec sens de rotation inversé => OK
    [angles_config_2.txt]
2019-06-01 Mouvements avec gyro du Nunchuck
2019-06-02 Cleanup documentation
    [hexapod-parameters.dwg]
2019-06-29 renommé hexapod_desktop_app + ajout lib_deps
    [angles_config_2.txt]
2019-07-04 Documentation algorithme
    [angles_config_2.txt, hexapod-parameters.dwg]
2019-07-04 Calc ZHOME + renommé d2 -> BP
    [angles_config_2.txt]
2019-07-05 Doc algorithme + cleanup
    [angles_config_2.txt, calc_zhome.ods]
2019-07-06 Nouvel algorithm (sympy) + speed test
    [angles_config_2.txt]
2019-07-07 Optimisation pour calmer les servos.
    [angles_config_2.txt]
2019-07-07 update servos incrémental
2019-07-09 shrink ranges dans desktop_app
    [angles_config_1.txt, angles_config_2.txt]
2019-07-16 Corrigé roll, pitch yaw
    [angles_config_2.txt]
2019-07-26 Nouvelle config de branchement pour debug ESP-Prog
2019-09-01 Nouveau servo MG90S
2022-05-07 Refactor + Debug units for PWM
    [angles_config_1.txt]
2023-02-03 Python implementation of algo 3
    [angles_config_1.txt, angles_config_2.txt, angles_with_config_1_cpp.txt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]
2023-02-04 Works on MicroPython v1.19.1
    [angles_with_config_1_py.txt]
2023-02-06 Python vs C++ comparison
    [angles_with_config_1_cpp.txt, angles_with_config_1_py.txt]
2024-04-14 Pin number correction for ATT
2024-04-20 Changed ATT pin cabling from IO35 to IO32.
2024-08-10 Conversion from DWG (DraftSight) to DXF (QCAD)
    [hexapod-parameters.dwg, hexapod-parameters.dxf]
2025-11-28 Update README with thesis and project references
    Added reference to Jakob Frabosilio's Master’s thesis and related resources.
2026-02-14 ajout ___stewart-platform-esp32.code-workspace
2026-03-20 Update README ESP32 purchase link

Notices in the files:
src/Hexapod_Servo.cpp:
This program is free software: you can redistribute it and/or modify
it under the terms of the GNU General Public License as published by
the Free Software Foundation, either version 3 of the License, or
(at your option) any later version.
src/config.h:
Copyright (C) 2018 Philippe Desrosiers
